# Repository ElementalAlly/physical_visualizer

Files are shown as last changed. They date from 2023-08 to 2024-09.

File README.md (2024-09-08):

# Arduino Stepper Motor-Driven Physical Music Visualizer

# Intro
This is a music visualizer that captures the frequencies of music playing through an audio jack output. It uses an Arduino for FFT processing and motor commands. Stepper motors are geared into a module that moves a bar up and down, according to their corresponding frequency.

A demo of the project is available [here](https://www.youtube.com/watch?v=0NpDhRlfrKM).

# Materials
 - Access to a 3D printer (I used an [Ender 3 Neo](https://www.creality.com/products/ender-3-neo-3d-printer), but other precise 3D printers should print fine.)
 - One Arduino MEGA R3 Board (I used [this one](https://www.amazon.com/ELEGOO-Compatible-Arduino-Projects-Compliant/dp/B01H4ZLZLQ))
 - One Breadboard (I used [this hat](https://www.amazon.com/HiLetgo-Prototype-Expansion-Breadboard-ProtoShield/dp/B00HHYBWPO/) to make it more compact, but a separate breadboard will work as well.)
 - 7 28BYJ-48 Motors ([This pack](https://www.amazon.com/28BYJ-48-ULN2003-Stepper-Driver-Arduino/dp/B07YRHX73L/) is cheap for 6. You will have to buy two to get enough for the visualizer.)
 - 7 4mm x 10mm x 4mm Bearings ([This pack](https://www.amazon.com/uxcell-MR104ZZ-Groove-Bearings-Shielded/dp/B082PSQZMX/) is good.)
 - 7 Micro Limit Switches (Get [this pack](https://www.amazon.com/HiLetgo-KW12-3-Roller-Switch-Normally/dp/B07X142VGC/).)
 - Soldering Iron and Solder ([This one](https://www.amazon.com/Soldering-Interchangeable-Adjustable-Temperature-Enthusiast/dp/B087767KNW/) should be fine.)
 - Multimeter (For testing connections. [This one](https://www.amazon.com/AstroAI-Digital-Multimeter-Voltage-Tester/dp/B01ISAMUA6/) would be fine.)
 - Wire Cutter and Stripper ([This one](https://www.amazon.com/WGGE-Professional-crimping-Multi-Tool-Multi-Function/dp/B073YG65N2/) is fine.)
 - 22 Gauge Solid-core Wire ([This pack](https://www.amazon.com/FIRMERST-Gauge-Solid-Tinned-Copper/dp/B0CCJ5YT3V/) should be enough.)
 - 1 Micro USB Power Adapter (I used [this one](https://www.amazon.com/WMYCONGCONG-Interface-Adapter-2-54mm-Breakout/dp/B082PDD79D/).)
 - 3.5 mm Audio Jack (I used [this one](https://www.amazon.com/Monoprice-3-5mm-Stereo-Plug-Cable/dp/B003NN1XZM/).)
 - 0.22 Micro-farad Capacitor ([This one](https://www.amazon.com/10pcs-0-22uF-Metallized-Polyester-Capacitors/dp/B00TX42OMQ/) should be fine.)
 - 2 100K Ohm Resistor ([This pack](https://www.amazon.com/100K-Resistor-Tolerance-Resistors-Resistance/dp/B0B4JDHXC9/) has enough.)

# Module Construction
Print out at least 7 of each component in 3DModels/basic_module. (I would recommend some spares of the two interface gears and the motor case. These snap somewhat easily.)

Put each of them together as shown in [this guide](https://github.com/ElementalAlly/physical_visualizer/raw/main/docs/moduleBuildingGuide.pdf).

# Wiring Tutorial
There are a few sections of wiring: Module Power, Module signals, and Input Reading.

## Input Reading
This circuit is the most complex out of all of them. While the rest power or signal components where the circuitry is already made, this is a circuit you will have to build yourself. The circuit looks like this:

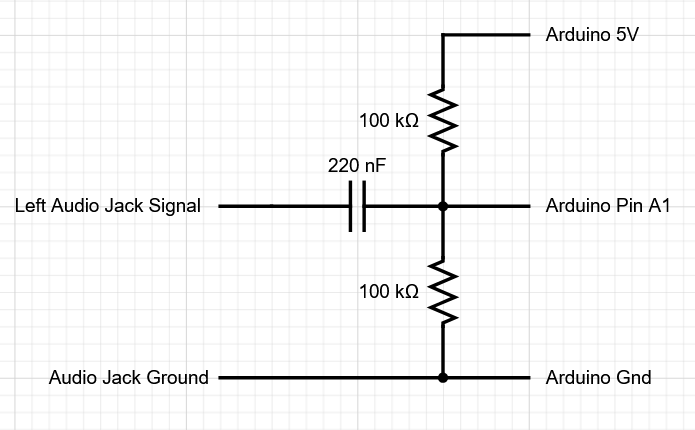
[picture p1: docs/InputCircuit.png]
Input circuit, check link below if it doesn't load


If the image doesn't load, check [this link](https://forum.arduino.cc/t/how-to-read-data-from-audio-jack/458301/3), and exclude R1.

This shifts the input from centering at 0 volts to centering at 2.5 volts, which allows the Arduino to read the entire input from its analog pins.

We use the left audio signal because it's most commonly used as mono.

The best way to get the audio signal and ground are to cut the audio extension cable in half and solder the two halves facing the same direction up on a prototype board, like the one seen on the end of the arduino hat I recommended. Then, solder the matching connections back together, and solder another two wires, one attaching to ground and the other attaching to the left signal. These can then be wired in the way of the diagram, and audio signal can be both received from a computer, and duplicated onto speakers with an audio jack.

From there, use the components from the materials to build the circuit!

## Module Power
This contains two major power circuits we need to take into account: Motor power and Limit Switch Power. There are two power sources for the entire system because 7 motors draw too much power and can disable the arduino accidentally. This is where the micro-USB power module comes into practice.

Power each motor using the Micro USB power adapter, as shown in the diagram. Use the same power source for all motors.

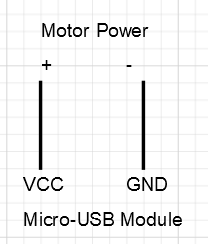
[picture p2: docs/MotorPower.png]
Motor is powered through the Micro USB Adapter


Connect each limit switch's ground to the ground of the arduino, as shown in this diagram:

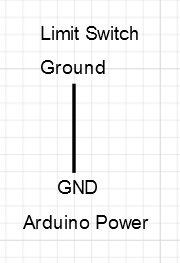
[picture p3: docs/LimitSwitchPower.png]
Limit switch ground is connected to the Arduino Ground


## Module Signals
When a motor is declared like this:

```
stepper stepper1(a, b, c, d, e)
```

Wire your motor and limit switch signal of module 1 like this:

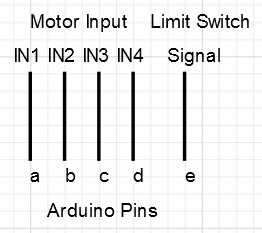
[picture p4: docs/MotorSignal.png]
a to IN1, b to IN2, c to IN3, d to IN4, e to Limit Switch Signal


For example, when you encounter:

```
stepper(7, 6, 5, 4, 3)
```

Wire IN1 to 7, IN2 to 6, IN3 to 5, IN4 to 4, and the Limit Switch Signal to 3.

All the motors' declarations are these:

```
stepper stepper1(7, 6, 5, 4, 3);
stepper stepper2(22, 24, 26, 28, 30);
stepper stepper3(23, 25, 27, 29, 31);
stepper stepper4(32, 34, 36, 38, 40);
stepper stepper5(33, 35, 37, 39, 41);
stepper stepper6(42, 44, 46, 48, 50);
stepper stepper7(43, 45, 47, 49, 51);
```

# Coding Tutorial
Download [Arduino IDE](https://www.arduino.cc/en/software) and open the physical_visualizer/physical_visualizer.ino file in it. Once everything has been wired, upload it and run it! Your modules should go up and down with the music that's played through the audio jack!

For the Approx_FFT Section, credit goes to abhilash_patel for the algorithm, and Klafyvel for some modifications and writing a blog post to show the algorithm compared to others. abhilash's original instructable with this code is here: <https://www.instructables.com/ApproxFFT-Fastest-FFT-Function-for-Arduino/>. Klafyvel's article is here: <https://klafyvel.me/blog/articles/fft-arduino/>, and their repo is here: <https://github.com/Klafyvel/AVR-FFT/tree/main>.

The sampling frequency, the number of samples per FFT, and the way the code groups the frequency buckets, make the individual bars react to approximately these following frequencies:

```
stepper1: 60 Hz -> 120 Hz
stepper2: 120 Hz -> 250 Hz
stepper3: 250 Hz -> 500 Hz
stepper4: 500 Hz -> 1000 Hz
stepper5: 1000 Hz -> 2000 Hz
stepper6: 2000 Hz -> 4000 Hz
stepper7: 4000 Hz -> 8000 Hz
```

This is limited to 8000 Hz because of the arduino platform having a cpu that isn't fast enough to sample at a fast enough rate to detect higher frequencies.

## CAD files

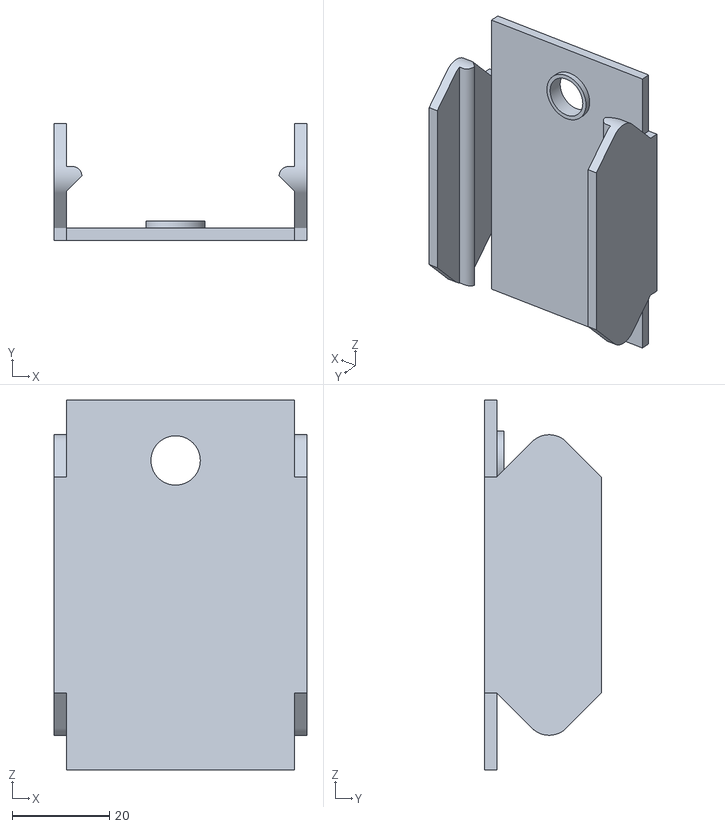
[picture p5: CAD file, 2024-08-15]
3DModels/basic_module/ModuleCase.stl
52.1 x 24.1 x 76.2

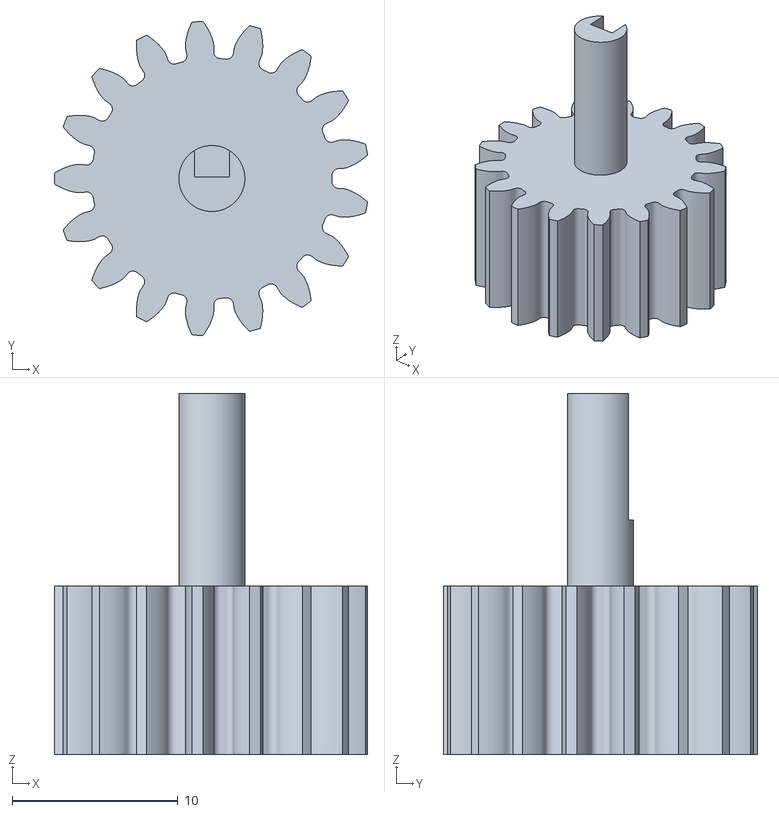
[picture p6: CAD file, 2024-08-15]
3DModels/basic_module/bigInterface.stl
18.9 x 19.0 x 21.8

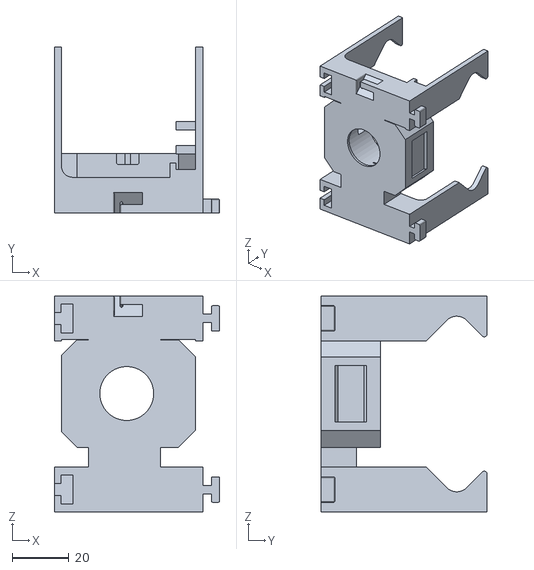
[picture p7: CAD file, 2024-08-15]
3DModels/basic_module/MotorCase.stl
58.6 x 58.9 x 76.5

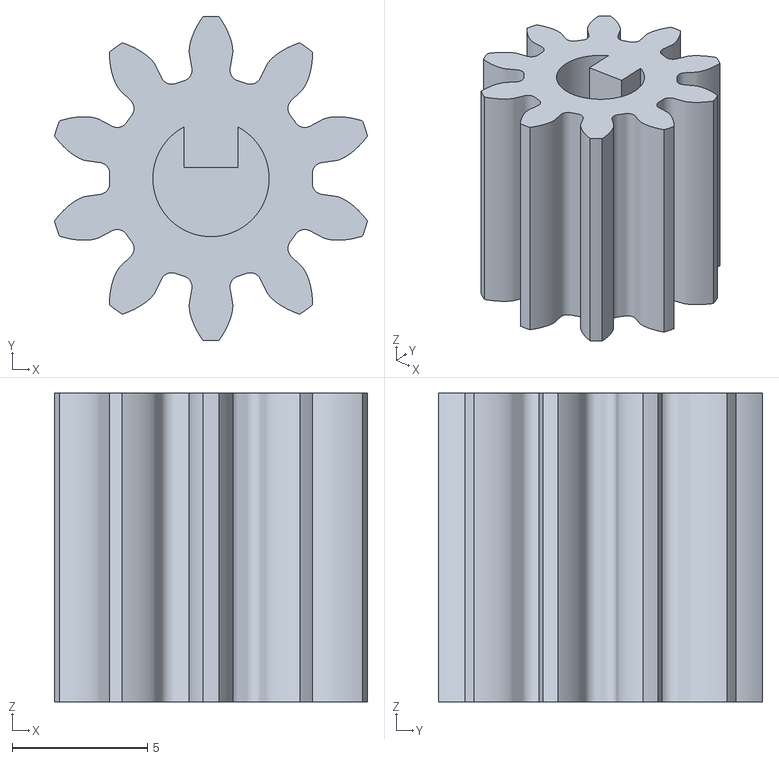
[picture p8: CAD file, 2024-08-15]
3DModels/basic_module/smallInterface.stl
11.6 x 12.0 x 11.4

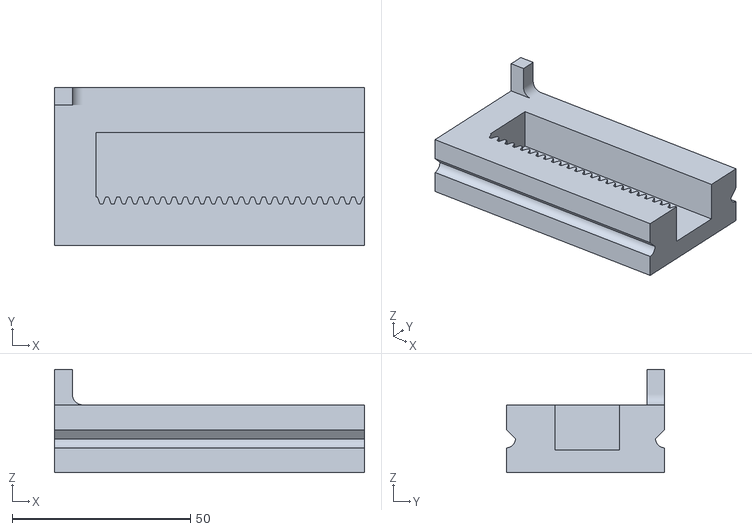
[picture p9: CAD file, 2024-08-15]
3DModels/basic_module/ModuleFace.stl
87.0 x 44.5 x 29.1

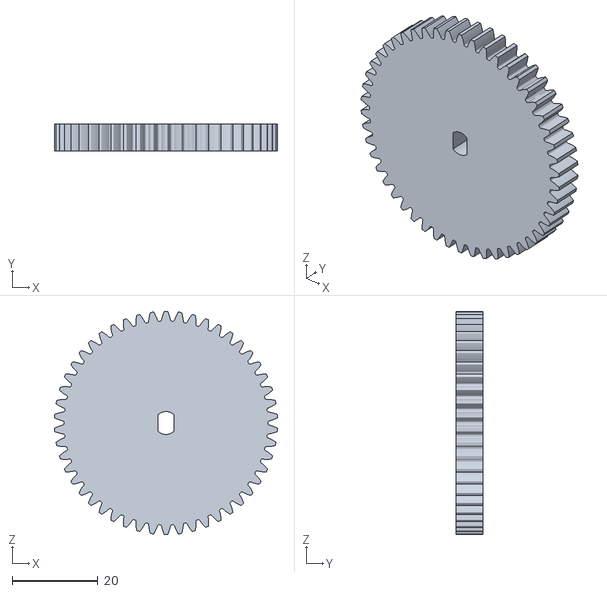
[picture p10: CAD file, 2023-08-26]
3DModels/basic_module/pinionGear.stl
51.9 x 6.35 x 52.0

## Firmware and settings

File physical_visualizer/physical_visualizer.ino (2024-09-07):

class highPriorityTicks { // parent class for time-sensitive ticks. Allows for a consistent framework for real-time systems.
  private:
    const static uint16_t tickAmount = 0;
    int prevTime = 0;
  public:
    virtual void tick() { // Represents one call through the system, checking if it should be called yet, then executing code to advance to the next state.
      uint16_t time = TCNT1;
      if (time - prevTime >= tickAmount) {
        prevTime = TCNT1;
      }
    }
};

// Tick system contains all of the steppers, so all steppers can be ticked in one function.

class tickSystem {
  private:
    static const int objectCap = 10;
    int numObjects = 0;
    int currentObject = 0;
    highPriorityTicks* objects[objectCap];
  public:
    tickSystem() {}

    void addObj(highPriorityTicks* tickObject) { // Adding an object to this system, to be ticked together.
      if (numObjects >= objectCap) {
        abort();
      }
      objects[numObjects] = tickObject;
      numObjects += 1;
    }

    void tickAll() { // Tick all objects in the system.
      for (int i = 0; i < numObjects; i++) {
        objects[i]->tick();
      }
    }
    
    void tickNext() {
      objects[currentObject]->tick();
      currentObject = (currentObject + 1) % numObjects;
    }
};

tickSystem systemTicks;

/* From the lookup data through the Fast RSS is not my code. I found this code through
this repo: https://github.com/Klafyvel/AVR-FFT, but the original code is from
this author: abhilash_patel, from this article: https://www.instructables.com/ApproxFFT-Fastest-FFT-Function-for-Arduino/

The only modification I made to this code is to attempt to tick my stepper motors throughout
the Fast Fourier Transform, to smoothly make my motors turn even through an FFT. */ 

/* ======== APPROXFFT CODE STARTS HERE || CREDIT TO abhilash_patel AND Klafyvel ======== */

//---------------------------------lookup data------------------------------------//
byte isin_data[128]=
{0,  1,   3,   4,   5,   6,   8,   9,   10,  11,  13,  14,  15,  17,  18,  19,  20,
22,  23,  24,  26,  27,  28,  29,  31,  32,  33,  35,  36,  37,  39,  40,  41,  42,
44,  45,  46,  48,  49,  50,  52,  53,  54,  56,  57,  59,  60,  61,  63,  64,  65,
67,  68,  70,  71,  72,  74,  75,  77,  78,  80,  81,  82,  84,  85,  87,  88,  90,
91,  93,  94,  96,  97,  99,  100, 102, 104, 105, 107, 108, 110, 112, 113, 115, 117,
118, 120, 122, 124, 125, 127, 129, 131, 133, 134, 136, 138, 140, 142, 144, 146, 148,
150, 152, 155, 157, 159, 161, 164, 166, 169, 171, 174, 176, 179, 182, 185, 188, 191,
195, 198, 202, 206, 210, 215, 221, 227, 236};
unsigned int Pow2[14]={1,2,4,8,16,32,64,128,256,512,1024,2048,4096};
byte RSSdata[20]={7,6,6,5,5,5,4,4,4,4,3,3,3,3,3,3,3,2,2,2};
//---------------------------------------------------------------------------------//

float Approx_FFT(int in[],int N,float Frequency) {
  uint16_t StartTime = TCNT1;
  int a,c1,f,o,x,data_max,data_min=0;
  long data_avg,data_mag,temp11;
  byte scale,check=0;

  data_max=0;
  data_avg=0;
  data_min=0;

  for(int i=0;i<12;i++) {                 //calculating the levels
    if(Pow2[i]<=N) {
      o=i;
    }
  }
  a=Pow2[o];
  int out_r[a];   //real part of transform
  int out_im[a];  //imaginory part of transform

  for(int i=0;i<a;i++) {                //getting min max and average for scalling
    out_r[i]=0; out_im[i]=0;
    data_avg=data_avg+in[i];
    if(in[i]>data_max){data_max=in[i];}
    if(in[i]<data_min){data_min=in[i];}
  }

  data_avg=data_avg>>o;
  scale=0;
  data_mag=data_max-data_min;
  temp11=data_mag;

  //scaling data  from +512 to -512

  if(data_mag>1024) {
    while(temp11>1024) {
      temp11=temp11>>1;
      scale=scale+1;
    }
  }

  if(data_mag<1024) {
    while(temp11<1024) {
      temp11=temp11<<1;
      scale=scale+1;
    }
  }


  if(data_mag>1024) {
    for(int i=0;i<a;i++) {
      in[i]=in[i]-data_avg;
      in[i]=in[i]>>scale;
    }
    scale=128-scale;
  }

  if(data_mag<1024) {
    scale=scale-1;
    for(int i=0;i<a;i++) {
      in[i]=in[i]-data_avg;
      in[i]=in[i]<<scale;
    }
    scale=128+scale;
  }

  for(int i=0;i<12;i++) {                 //calculating the levels
    if(Pow2[i]<=N) {
      o=i;
    }
  }

  systemTicks.tickAll();

  x=0;
  for(int b=0;b<o;b++) {                    // bit reversal order stored in im_out array
    c1=Pow2[b];
    f=Pow2[o]/(c1+c1);
    for(int j=0;j<c1;j++) {
      x=x+1;
      out_im[x]=out_im[j]+f;
      systemTicks.tickAll();
    }
  }

  for(int i=0;i<a;i++) {           // update input array as per bit reverse order
    out_r[i]=in[out_im[i]];
    out_im[i]=0;
    systemTicks.tickAll();
  }

  uint16_t EndTime = TCNT1;
  uint16_t eta = EndTime - StartTime;
  // Serial.print("FFT Init: ");
  // Serial.println(eta);

  int i10,i11,n1,tr,ti;
  float e;
  int c,s,temp4;
  for(int i=0;i<o;i++) {                                    //fft
    i10=Pow2[i];              // overall values of sine/cosine
    i11=Pow2[o]/Pow2[i+1];    // loop with similar sine cosine
    e=1024/Pow2[i+1];  //1024 is equivalent to 360 deg
    e=0-e;
    n1=0;
    systemTicks.tickAll();

    for(int j=0;j<i10;j++) {
      c=e*j;    //c is angle as where 1024 unit is 360 deg
      while(c<0) {
        c=c+1024;
      }
      while(c>1024) {
        c=c-1024;
      }

      n1=j;

      systemTicks.tickAll();

      for(int k=0;k<i11;k++) {
        temp4=i10+n1;
        if(c==0) {
          tr=out_r[temp4];
          ti=out_im[temp4];
        }
        else if(c==256) {
          tr= -out_im[temp4];
          ti=out_r[temp4];
        }
        else if(c==512) {
          tr=-out_r[temp4];
          ti=-out_im[temp4];
        }
        else if(c==768) {
          tr=out_im[temp4];
          ti=-out_r[temp4];
        }
        else if(c==1024) {
          tr=out_r[temp4];
          ti=out_im[temp4];
        }
        else {
          tr=fast_cosine(out_r[temp4],c)-fast_sine(out_im[temp4],c);            //the fast sine/cosine function gives direct (approx) output for A*sinx
          ti=fast_sine(out_r[temp4],c)+fast_cosine(out_im[temp4],c);
        }

        systemTicks.tickAll();

        out_r[n1+i10]=out_r[n1]-tr;
        out_r[n1]=out_r[n1]+tr;
        if(out_r[n1]>15000 || out_r[n1]<-15000) {
          check=1;
        }   //check for int size, it can handle only +31000 to -31000,

        out_im[n1+i10]=out_im[n1]-ti;
        out_im[n1]=out_im[n1]+ti;
        if(out_im[n1]>15000 || out_im[n1]<-15000) {
          check=1;
        }

        n1=n1+i10+i10;
      }
    }

    if(check==1){                                             // scalling the matrics if value higher than 15000 to prevent varible from overflowing
      for(int i=0;i<a;i++) {
        out_r[i]=out_r[i]>>1;
        out_im[i]=out_im[i]>>1;
        systemTicks.tickAll();
      }
      check=0;
      scale=scale-1;                 // tracking overall scalling of input data
    }
  }


  if(scale>128) {
    scale=scale-128;
    for(int i=0;i<a;i++) {
      out_r[i]=out_r[i]>>scale;
      out_im[i]=out_im[i]>>scale;
      systemTicks.tickAll();
    }
    scale=0;
  }                                                   // revers all scalling we done till here,
  else {
    scale=128-scale;
  }                             // in case of nnumber getting higher than 32000, we will represent in as multiple of 2^scale

  /*
  for(int i=0;i<a;i++)
  {
    Serial.print(out_r[i]);Serial.print("\t");                    // un comment to print RAW o/p
    Serial.print(out_im[i]);
    Serial.print("i");Serial.print("\t");
    Serial.print("*2^");Serial.println(scale);
  }
  */

  //---> here onward out_r contains amplitude and our_in conntains frequency (Hz)
  int fout,fm,fstp;
  float fstep;
  fstep=Frequency/N;
  fstp=fstep;
  fout=0;fm=0;

  for(int i=1;i<Pow2[o-1];i++) {               // getting amplitude from compex number
    /* Second part modified by klafyvel to output the result in the
    input array.
    */
    //out_r[i]=fastRSS(out_r[i],out_im[i]);
    in[i]=fastRSS(out_r[i],out_im[i]);
    // Approx RSS function used to calculated magnitude quickly

    out_im[i]=out_im[i-1]+fstp;
    if (fout<in[i]){
      fm=i; fout=in[i];
    }
    /* End of the second part modified by klafyvel. */

    systemTicks.tickAll();

    // un comment to print Amplitudes (1st value (offset) is not printed)
    // Serial.println(out_r[i]);// Serial.print("\t");
    //Serial.print("*2^");Serial.println(scale);
  }


  float fa,fb,fc;
  fa=out_r[fm-1];
  fb=out_r[fm];
  fc=out_r[fm+1];
  fstep=(fa*(fm-1)+fb*fm+fc*(fm+1))/(fa+fb+fc);

  return(fstep*Frequency/N);
}

//---------------------------------fast sine/cosine---------------------------------------//

int fast_sine(int Amp, int th) {
  int temp3,m1,m2;
  byte temp1,temp2, test,quad,accuracy;
  accuracy=5;    // set it value from 1 to 7, where 7 being most accurate but slowest
               // accuracy value of 5 recommended for typical applicaiton
  while(th>1024) {
    th=th-1024;
  }   // here 1024 = 2*pi or 360 deg
  while(th<0) {
    th=th+1024;
  }
  quad=th>>8;

  if(quad==1) {
    th=512-th;
  }
  else if(quad==2) {
    th= th-512;
  }
  else if(quad==3) {
    th= 1024-th;
  }

  temp1= 0;
  temp2= 128;     //2 multiple
  m1=0;
  m2=Amp;

  temp3=(m1+m2)>>1;
  Amp=temp3;
  for(int i=0;i<accuracy;i++) {
    test=(temp1+temp2)>>1;
    temp3=temp3>>1;
    if(th>isin_data[test]) {
      temp1=test; Amp=Amp+temp3; m1=Amp;
    }
    else if(th<isin_data[test]) {
      temp2=test; Amp=Amp-temp3; m2=Amp;
    }
  }

  if(quad==2) {
    Amp= 0-Amp;
  }
  else if(quad==3) {
    Amp= 0-Amp;
  }
  return(Amp);
}

int fast_cosine(int Amp, int th) {
  th=256-th;  //cos th = sin (90-th) formula
  return(fast_sine(Amp,th));
}

//--------------------------------------------------------------------------------//


//--------------------------------Fast RSS----------------------------------------//
int fastRSS(int a, int b) {
  if(a==0 && b==0){return(0);}
  int min,max,temp1,temp2;
  byte clevel;
  if(a<0){a=-a;}
  if(b<0){b=-b;}
  clevel=0;
  if(a>b) {
    max=a;min=b;
  }
  else {
    max=b;min=a;
  }

  if(max>(min+min+min)) {
    return max;
  }
  else {
    temp1=min>>3; if(temp1==0){temp1=1;}
    temp2=min;
    while(temp2<max) {
      temp2=temp2+temp1;clevel=clevel+1;
    }
    temp2=RSSdata[clevel];temp1=temp1>>1;
    for(int i=0;i<temp2;i++) {
      max=max+temp1;
    }
    return(max);
  }
}
//--------------------------------------------------------------------------------//

/* ======== APPROXFFT CODE ENDS HERE || CREDIT TO abhilash_patel AND Klafyvel ======== */

// Clearing and setting bits
#ifndef cbi
#define cbi(sfr, bit) (_SFR_BYTE(sfr) &= ~_BV(bit))
#endif
#ifndef sbi
#define sbi(sfr, bit) (_SFR_BYTE(sfr) |= _BV(bit))
#endif

const int samples = 512;
const int samplingFrequency = 16000;

const int stepsPerRevolution = 2038;
const int maxAngleDegrees = 75;
const uint16_t maxTicks = (uint16_t)((double)stepsPerRevolution / 360 * maxAngleDegrees);

int vReal[samples];
uint16_t amplitudes[samples];

class stepper: public highPriorityTicks {
  private:
    const int stepperStates[4][4] = {
      {1, 1, 0, 0},
      {0, 1, 1, 0},
      {0, 0, 1, 1},
      {1, 0, 0, 1}
    };
    const static uint16_t tickAmount = 37000;
    const static int limitSwitchBounceTolerance = 10;
    int prevTime = 0;
    int target;
    int direction;
    int currentTick;
    int currentState;
    int ports[4];
    int limitSwitchPin;

    bool atTarget() { // Checks if the motor is at the target.
      return currentTick == target;
    }

  public:
    stepper(int port1, int port2, int port3, int port4, int limitPin) { // Initializes the motor. Pins are initialized for output, and low is written. The limit switch's pin is initialized to input. The stepper is then added to the tick system.
      target = 0;
      direction = 0;
      currentTick = 0;
      currentState = 0;
      ports[0] = port1;
      ports[1] = port2;
      ports[2] = port3;
      ports[3] = port4;
      limitSwitchPin = limitPin;
      for (int i=0; i<4; i++) {
        pinMode(ports[i], OUTPUT);
        digitalWrite(ports[i], LOW);
      }
      pinMode(limitSwitchPin, INPUT_PULLUP);
      systemTicks.addObj(this);
    }

    void setTarget(int newTarget) { // Sets the new target for the motor to go to. If the motor has started to move up and a higher peak is detected, the motor will move to the higher peak, and vice versa. Less extreme amplitudes are ignored.
      if (direction == 0) {
        target = newTarget;
        if (newTarget < currentTick) {
          direction = -1;
        }
        if (newTarget > currentTick) {
          direction = 1;
        }
      }
      if (direction == 1) {
        target = max(target, newTarget);
      }
      if (direction == -1) {
        target = min(target, newTarget);
      }
    }

    void reset() { // Resets the module's position to the bottom, just before the limit switch is pressed down.
      target = -stepsPerRevolution;
      int count = 0;
      while (count < limitSwitchBounceTolerance) {
        tick();
        currentTick = 0;
        if (digitalRead(limitSwitchPin) == LOW) {
          count++;
        }
        else {
          count = 0;
        }
      }
      Serial.println("Limit switch down");
      target = stepsPerRevolution;
      count = 0;
      while (count < limitSwitchBounceTolerance) {
        tick();
        currentTick = 0;
        if (digitalRead(limitSwitchPin) == HIGH) {
          count++;
        }
        else {
          count = 0;
        }
      }
      Serial.println("Limit switch up");
      currentTick = -50;
      setTarget(0);
    }

    void tick() override { // If enough time has passed, steps the motor once towards the target. If the target has been reached, direction is reset.
      uint16_t time = TCNT1;
      if (time - prevTime >= tickAmount) {
        if (digitalRead(limitSwitchPin) == LOW) {
          currentTick = -50;
        }
        if (currentTick < target) {
          currentState = (currentState + 1) % 4;
          for (int i=0; i<4; i++) {
            digitalWrite(ports[i], stepperStates[currentState][i]);
          }
          currentTick += 1;
        }
        else if (currentTick > target) {
          currentState = (currentState + 3) % 4;
          for (int i=0; i<4; i++) {
            digitalWrite(ports[i], stepperStates[currentState][i]);
          }
          currentTick -= 1;
        }
        else if (atTarget()) {
          direction = 0;
        }
        prevTime = TCNT1;
      }
    }
};

/* === Testing data, defined by the sum of the sin waves defined by these parameters === */

/* const double signal1Freq = 440;
const double signal1Cycles = (((samples-1) * signal1Freq) / samplingFrequency);
const double signal1Amp = 511;
const double signal2Freq = 1000;
const double signal2Cycles = (((samples-1) * signal2Freq) / samplingFrequency);
const double signal2Amp = 0;
const double signal3Freq = 2000;
const double signal3Cycles = (((samples-1) * signal3Freq) / samplingFrequency);
const double signal3Amp = 0;
const double twoPi = 6.283185307; */

/* === Testing data done === */

/* === These are sampler states. GET_SAMPLE means that sampler only gets a sample from the mic, where FFT means that an FFT has been run. === */

#define GET_SAMPLE 0
#define FFT 1

/* === Sampler state end === */

class sampler {
  private:
    const static uint16_t tickAmount = 600; // 726;
    int prevTime = 0;
    int numSamples = 0;
    int pin;
  public:
    sampler(int inPin) { // Initializes the sampler to read from the inPin.
      pin = inPin;
      pinMode(inPin, INPUT);
    }

    int tick() { // If enough time has passed, record the state of the pin. If enough samples have been collected, run the FFT and return the FFT state.
      uint16_t time = TCNT1;
      if (time - prevTime >= tickAmount) {
        // Serial.println(time - prevTime);
        vReal[numSamples] = analogRead(pin) - 512;
        // Debugging, using the sum of the waves defined by the frequencies above the sampler class
        // vReal[numSamples] = int16_t(signal1Amp * (sin(numSamples * (twoPi * signal1Cycles) / samples)) + signal2Amp * (sin(numSamples * (twoPi * signal2Cycles) / samples)) + signal3Amp * (sin(numSamples * (twoPi * signal3Cycles) / samples)));
        numSamples += 1;
        prevTime = TCNT1;
        if (numSamples >= samples) {
          uint16_t startTime = TCNT1;
          Approx_FFT(vReal, samples, 44100);
          uint16_t endTime = TCNT1;
          uint16_t eta = endTime - startTime;
          numSamples = 0;
          return FFT;
        }
      }
      return GET_SAMPLE;
    }
};

stepper stepper1(7, 6, 5, 4, 3);
stepper stepper2(22, 24, 26, 28, 30);
stepper stepper3(23, 25, 27, 29, 31);
stepper stepper4(32, 34, 36, 38, 40);
stepper stepper5(33, 35, 37, 39, 41);
stepper stepper6(42, 44, 46, 48, 50); 
stepper stepper7(43, 45, 47, 49, 51);
sampler mySampler(A1);

void setup() { // Initialize registers, and reset all the modules.
  Serial.begin(115200);
  while (!Serial) {}
  Serial.println("Setup");
  delay(1000);
  Serial.println("---------");

  // setting up the cpu clock to be read for real-time systems
  TCCR1A = 0;
  TCCR1B = 1;

  // Setting the ADC clock circuit multiplier to 16, for faster Analog Reads
  sbi(ADCSRA,ADPS2);
  cbi(ADCSRA,ADPS1);
  cbi(ADCSRA,ADPS0);

  Serial.println();
  Serial.println("Reset started");
  Serial.println("===========");
  stepper1.reset();
  stepper2.reset();
  stepper3.reset();
  stepper4.reset();
  stepper5.reset();
  stepper6.reset();
  stepper7.reset();
  Serial.println("===========");
  Serial.println("Reset completed");
  delay(1000);
}

int status = 0;

void printList(int* list, int length) { // print all entries of a list of length "length".
  for (int i = 0; i < length; i++) {
    Serial.print(list[i]);
    Serial.print("     ");
  }
  Serial.println();
}

void loop() { // Tick all motors, and tick the sampler. If the FFT has been executed, find the peaks in various ranges that scale exponentially, then sets the motors targets to the adjusted peaks.
  systemTicks.tickNext();
  status = mySampler.tick();
  if (status == FFT) {

    int startIndex = 2;
    int endIndex = 4;
    uint16_t peaks[7];
    int targets[7];
    int maxIndex[7];
    double factors[7] = {(double)maxTicks / 3000.0, (double)maxTicks / 8000.0, (double)maxTicks / 8000.0, (double)maxTicks / 6000.0, (double)maxTicks / 4000.0, (double)maxTicks / 3000.0, (double)maxTicks / 2000.0};
    uint16_t floors[7] = {0, 0, 0, 0, 0, 0, 0};

    for (int i = 0; i < 7; i++) { // make 7-bucket function
      int max = 0;
      for (int j = startIndex; j < endIndex; j++) {
        if (max < vReal[j]) {
          max = vReal[j];
          maxIndex[i] = j;
        }
      }
      peaks[i] = max;
      if (peaks[i] > floors[i]) {
        targets[i] = (peaks[i] - floors[i]) * factors[i];
      }
      else {
        targets[i] = 0;
      }
      if (targets[i] > maxTicks) {
        targets[i] = maxTicks;
      }
      startIndex = endIndex;
      endIndex *= 2;
    }

    /* Serial.print("Raw: ");
    printList(peaks, 7); */
    /* Serial.print("Targets: ");
    printList(targets, 7); */
      
    stepper1.setTarget(targets[0]);
    stepper2.setTarget(targets[1]);
    stepper3.setTarget(targets[2]);
    stepper4.setTarget(targets[3]);
    stepper5.setTarget(targets[4]);
    stepper6.setTarget(targets[5]);
    stepper7.setTarget(targets[6]);
  }
}

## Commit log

2023-07-21 initial commit, one motor
2023-08-08 ticks during fft working, fft still broken
    [physical_visualizer.ino]
2023-08-08 Repaired FFT, add motor 2
2023-08-14 7 Motors
2023-08-14 Initial 3d Models
    [ModuleCase.stl, ModuleFace.stl, ModuleInterfaceGear.stl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]
2023-08-26 module v2
    [ModuleCase.stl, ModuleFace.stl, ModuleInterfaceGear.stl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]
2024-06-19 Limit switch present, module movement figured out
2024-06-25 Many things fixed
    - Spacing is corrected
    - Reset implemented
    - Scaling implemented
    [physical_visualizer.ino]
2024-08-03 Motors theoretically all working :)
2024-08-06 Working motors! Fixed Abort!
    [physical_visualizer.ino]
2024-08-15 Basic Module built, V8
    Other versions were iterated through locally.
    [ModuleCase.stl, ModuleFace.stl, ModuleInterfaceGear.stl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]
2024-08-27 Making sampler frequency correct and run faster
    [physical_visualizer.ino]
2024-08-27 Reset when limit switch down
    [physical_visualizer.ino]
2024-08-27 Initial README Created. Needs Wiring and Mechanics.
2024-08-29 Make motors spin until Limit Switch
